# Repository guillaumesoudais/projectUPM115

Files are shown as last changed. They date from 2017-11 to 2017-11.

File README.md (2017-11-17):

# Escaping Robot (UPM115 Project)

## Introduction

The aim of the project is to make a robot that is able to find the exit of a maze.
The strategy of the robot is to take the direction that is on the most on the left.
For that we will use a ultrasonic sensor mounted on a servo motor to find this direction and two motors for the two wheels of the robot.
If we had enough time, we would have made this robot to map the maze it’s in.

## General architecture of the project

The project will have the following modules :
- The movement module which is the module that makes the robot moving. Its entry points are the direction and speed commands
- The sonar module which detects obstacles. Its entry points are angles for the servo motor and it must send the distance of the obstacle to the command module
- The command module which receive information from the sonar and decide of the direction and speed of the robot as well as its sonar orientation
Optional modules (if we have had enough time) :
- The mapping module : receives information from the servo and the command module to record obstacle position

## Stages of the project

To realise this project we will use an incremental method. Below are the stages of the project:
- Realizing the movement module : add a few tests function with recorded moves to verify that the module is working
- Realizing the sonar module : same principle as previous step
- Realizing the command module
Optional steps (if we have had enough time) :
- Mapping the path of the robot : be able to deduce the path of the robot from the commands of the wheels (admitting it will not slide)
- Mapping the obstacle : from the position of the robot obtained in the previous step and the position of the obstacle, mapping the obstacles of the maze
- Find a shorter path : after mapping the path of the robot, deduce a shorter path by eliminating dead-ends

## Realisation of the project

### Material needed
- Arduino uno
- Ultrasonic sensor
- Batteries
- DC motors
- Servo

### Construction
Schematics of the connection for the robot.
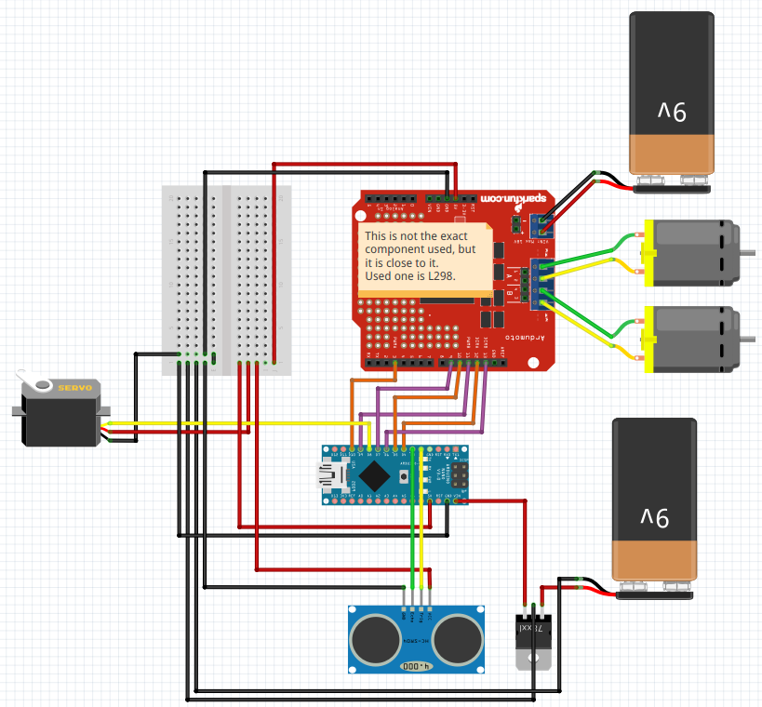
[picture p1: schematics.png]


[schematics]: https://github.com/guillaumesoudais/projectUPM115/blob/master/schematics.png "Schematics"

Picture of the robot with all its messy wiring.

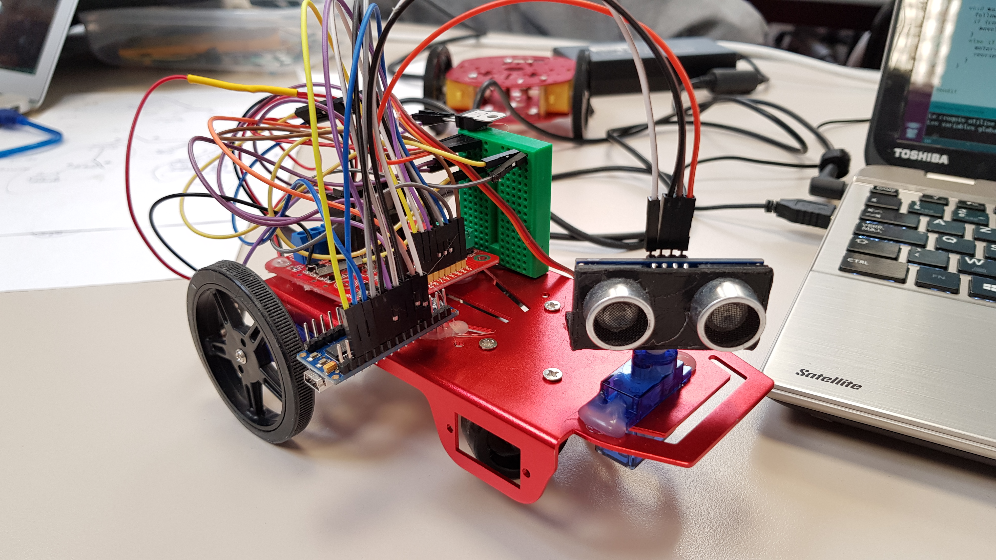
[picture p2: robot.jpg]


[robot]: https://github.com/guillaumesoudais/projectUPM115/blob/master/robot.jpg "Schematics"

Here is a video of the final version of the project.

IMAGE ALT TEXT HERE (https://www.youtube.com/watch?v=FyLfuLq4kfI)

### Code structure

the main code is in mazeRobot.ino where we initialize the constant needed (e.g. pins).
Then we have three modules :
- sonar.h  that commands the sonar
- motors.h that commands the wheels
- brain.h that is where the escaping strategy is implemented.

#### Sonar

The sonar has a servo for attribute which can be commanded through the *setAngle* function.
It has also an *udpdate()* function that read the angle of the Servo and calculate the distance.

```{cpp}
/* sending the instructon to measure the distance */
digitalWrite(triggerPin, HIGH);
delayMicroseconds(10);
digitalWrite(triggerPin, LOW);

/* measuring time between sending and receiving of the impulsion */
long measure = pulseIn(echoPin, HIGH, MEASURE_TIMEOUT);

/* calculating the distance */
distance = measure / 2.0 * SOUND_SPEED;
distanceList[index] = distance;
index ++;
if (index == LENGTH) {
    index = 0;
}

float d = 0;
for (int i = 0; i < LENGTH; i++) {
    d += distanceList[i];
}
mean = d / LENGTH;
```

*mean* is an attribute that stores the mean of the ten last value (because sometimes values are not accurate).
*distance* is an attribute that stores the last value.
*distanceList* is an array that stores the ten last values.

the function *longUpdate* does ten *update* in order to renew the *distanceList*

#### motors

The motors controls the two motors. It can activate them together or separately in both direction of rotation.

It has a specific function : *slowMove*

Because we couldn't use the motor directly with low speed. We only had a 9V battery, so the torque was to high to go under 128 over 255 possible values of speed.

Then to recreate a low speed movement, we decided to make the wheels turn briefly and then stop in a 6 miliseconds loop.

We have the following function :

```{cpp}
void slowMove(int n,boolean forward=true) {
    move(255, forward);
    delay(n);
    stop();
    delay(6 - n);
}
```

then we have six different speeds with n going from 1 to 6.

#### brain

The brain has a object Motors and a Sonar as attributes, so it can command them.

But before looking at the code, we must understand the strategy used.

##### Escaping strategy

The strategy used to escape a maze is very simple.

Since the robot only knows what is around him and what he has been through, we can't use algorithm such as Dijkstra to find the shortest path.

So the path would not be optimal.

The strategy is to *always take the direction that is most at right*.

In mazes where the entry point and the exit are placed on the outside of the maze, this strategy doesn't suffer from loops.

In mazes where the arrival is not an exit but a point inside the maze, then loops can alter the resolution. But we won't consider this case here.

As a matter of fact, considering the amount of time we were given, we only made a robot that is able to follow a wall at its right side.

We've been through several strategies :
- first, we thought about dealing only with mazes with right-angled corners. Then we would only had to *make rotations of 90 degres* and moving forward. But the motors weren't turning at the exact same speed and a calibration would have taken too much time.
- then, we decided to use the same strategies as above but with *smaller angles* giving the robot the opportunity to easily correct the direction. So the robot was successively looking at his right, in front of him and at his left and turn from a little angle according to what he saw or moving forward and loop.
- Another technique was to always move forward and to increase the speed of one of the wheel according to the distance measured on the right. But the sonar was less efficient in movement.

So we finally used the second technique.

The strategy is basically :
- look on the right
- if there is no close obstacle on the right
    - turn on right of an 90 degres angle
    - if there is no obstacle, we move forward (function *pasEnAvant*)
    - if there is an obstacle or if it's been 5 time we turned right (meaning there is no wall near) we move forward until there is a wall (function *moveToWall()*)
- if there is an obtacle on the right
    - we look in front of the robot
    - while there is an obstacle in front of him 
        - the robot turn slightly left
        - the sonar update
    - then (there is no more obstacle in front of him) we move forward from a small distance (function *pasEnAvant*)

Here is a code of the main function *mainish* that does the above strategy :

```{cpp}
void mainish() {
    sonar->setAngle(0);
    sonar->longUpdate();
    if (sonar->mean > MARGIN) {
    motor->turnRight(1, quartTour);
    sonar->update();
    if (sonar->distance < MARGIN || counter == 5) {
        moveToWall();
        counter = 0;
    }
    else {
        pasEnAvant();
        counter++;
    }
    }
    else {
    counter = 0;
    int angle = S_ANGLE;
    sonar->setAngle(90);
    sonar->update();
    while (sonar->distance < MARGIN) {
        motor->turnLeft(1, smallTour);
        angle += S_ANGLE;
        sonar->update();
    }
    pasEnAvant();          
    }
}
```

Let's now take a look at *pasEnAvant* :

```{cpp}
void pasEnAvant() {
    sonar->setAngle(90);
    for (int i =  0; i < pas ; i++) {
        sonar->update();
        if (sonar->distance < 100) {
            break;
        }
        motor->slowMove(vit);
    }
}
```

it goes forward of a fixed distance linked to the constant *pas* and then it stops. 

If it gets close from an obstacle before reaching the fixed distance, it also stops.

We also have the function *moveToWall* :

```{cpp}
void moveToWall() {
    sonar->setAngle(90);
    sonar->update();
    while (sonar->distance > MARGIN) {
        motor->slowMove(vit);
        sonar->update();
    }
} 
```

It goes forward until it meets an obstacle. 

## Possible improvements

- The body of the robot is too long. It is possible that the sonar passes in front of a wall and that the tail is still in front of the wall. So when it tries to turn, it hits the wall. In order to improve, the sonar should be above the rotation axis, so between the wheels. We tried to stick with a small body robot but could not fit everything on it, and the motors had a too high consumption of energy.
- The moves of the robot when there were no obstacle around him were a bit hazardous. An idea was to make an *init() function* in the class *Brain* which would be lauched by the *setup* in order to find a wall and then follow it. We tried it but we hadn't the time to find a efficient version of this function because the sonar sometimes gets preposterous values.
- The movements of the robot weren't precise. We could have write a calibration routine in the setup function during with the robot would have calibrate himself by finding a wall and rolling toward it and measuring the distance with the sonar.
- With a calibrated robot, we could have mapped the maze in order to find a shorter way later
- We wrote a *getMinimumAngle* function that would have allowed us to find the angle for which the sonar measure the minimal distance. This would have helped to locate the obstacle and get a more precise measure of its distance. We didn't use it because it slowed down the robot

```{cpp}
int getMinimumAngle(int max, int pas) {
    setAngle(max);
    longUpdate();
    float dist = distance;
    int res = max;
    for (int a = max - pas; a >= 0; a -= pas) {
        setAngle(a);
        longUpdate();
        if (distance < dist) {
        res = a;
        dist = distance;
        }
    }
    setAngle(res);
    return res;
}
```

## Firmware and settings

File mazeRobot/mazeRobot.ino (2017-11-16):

#include <Servo.h>
#include "sonar.h"
#include "motors.h"
#include "brain.h"

Motors *motors;
Sonar *sonar;
Brain *brain;
int enA = 10;
int enB = 9;
int fwdA = 4;
int bwdA = 5;
int fwdB = 6;
int bwdB = 7;
int startSpeed = 128;
Servo myServo;
int pinServo = 8;
int trigger = 2;
int echo = 3;
boolean isRolling = false;
int time;
int delta = 500;

void setup() {
  motors = new Motors(enA, fwdA, bwdA, enB, fwdB, bwdB);
  sonar = new Sonar(myServo, pinServo, trigger, echo);
  brain = new Brain(sonar, motors);


  pinMode(trigger, OUTPUT);
  digitalWrite(trigger, LOW);
  pinMode(echo, INPUT);
  pinMode(enA, OUTPUT);
  pinMode(enB, OUTPUT);
  pinMode(fwdA, OUTPUT);
  pinMode(fwdB, OUTPUT);
  pinMode(bwdA, OUTPUT);
  pinMode(bwdB, OUTPUT);
  pinMode(pinServo, OUTPUT);
}

void loop() {
  brain->mainish();

}

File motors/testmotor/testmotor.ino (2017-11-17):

int enA = 10;
int enB = 9;//prob
int fwdA = 4;
int bwdA = 5;
int fwdB = 6;
int bwdB = 7;
int speed = 128;



void move(int speed, boolean forward = true) {
  
  analogWrite(enB, speed);
  analogWrite(enA, speed);
  digitalWrite(fwdA, forward);
  digitalWrite(fwdB, forward);
  digitalWrite(bwdA, !forward);
  digitalWrite(bwdB, !forward);
}

void slowMove2(int n){
  for (int i = 0; i<n;i++){
    move(speed);
    delay(10);
    stop();
    delay(50);
  }
}

void slowMove(int n){
  move(255);
  delay(50);
  move(32);
  delay(1000);
  stop();
  
}

void stop() {
  analogWrite(enA, 0);
  analogWrite(enB, 0);
  digitalWrite(fwdA, 0);
  digitalWrite(fwdB, 0);
  digitalWrite(bwdA, 0);
  digitalWrite(bwdB, 0);
}

void turn(boolean left, int speed) {
  analogWrite(enA, speed);
  analogWrite(enB, speed);
  digitalWrite(fwdA, !left);
  digitalWrite(fwdB, left);
  digitalWrite(bwdA, left);
  digitalWrite(bwdB, !left);
}

void turnLeft(int speed) {
  turn(true, speed);
}

void turnRight(int speed) {
  turn(false, speed);
}

void setup() {
  // put your setup code here, to run once:
pinMode(enA, OUTPUT);
  pinMode(enB, OUTPUT);
  pinMode(fwdA, OUTPUT);
  pinMode(bwdA, OUTPUT);
  pinMode(fwdB, OUTPUT);
  pinMode(bwdB, OUTPUT);
  
}
void loop() {
  // put your main code here, to run repeatedly:
  slowMove(20);
  delay(1000);
  
}

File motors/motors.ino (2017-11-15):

class Motors {
    int enA;    // enable for motor A (left)
    int fwdA;   // forward pin for motor A
    int bwdA;   // backward pin for motor A

    int enB;    // enable for second motor B (right)
    int fwdB;   // forward pin for motor B
    int bwdB;    // backward pin for motor B

    void move(int speed, boolean forward = true) {
      analogWrite(enA, speed);
      analogWrite(enB, speed);
      analogWrite(fwdA, forward);
      analogWrite(fwdB, forward);
      analogWrite(bwdA, !forward);
      analogWrite(bwdB, !forward);
    }

    void stop() {
      analogWrite(enA, 0);
      analogWrite(enB, 0);
      analogWrite(fwdA, 0);
      analogWrite(fwdB, 0);
      analogWrite(bwdA, 0);
      analogWrite(bwdB, 0);
    }

    void turn(boolean left, int speed) {
      analogWrite(enA, speed);
      analogWrite(enB, speed);
      analogWrite(fwdA, !left);
      analogWrite(fwdB, left);
      analogWrite(bwdA, left);
      analogWrite(bwdB, !left);
    }

    void turnLeft(int speed) {
      this.turn(true, speed);
    }

    void turnRight(int speed) {
      this.turn(false, speed);
    }

    void slowMove(int s) {
      this.move(128);
      delay(20);
      this.move(s);
    }
}

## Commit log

2017-11-15 programme de sonar
2017-11-15 Creating and implementing the sonar class
2017-11-15 implemented class for controlling motors
2017-11-15 wiring connexion
    [wiring.fzz]
2017-11-15 first test with sensor
2017-11-16 petit bout de code
2017-11-16 ajout de la classe brain
2017-11-17 nice schematics
    [wiring.fzz]
